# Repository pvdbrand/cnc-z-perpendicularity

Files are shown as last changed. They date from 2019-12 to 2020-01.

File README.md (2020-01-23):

# Automatically calibrating a CNC

## What's this?

The repository contains a Python script to automatically determine how perpendicular the Z axis of a CNC machine is, using just a feeler gauge and a touch probe.

This repository also contains a simulator (written in Rust) to make sure that the movements and calculations in the Python script are actually correct.

## How to use it

### Hardware

1. Build the arm:
   1. 3D print the [arm](https://github.com/pvdbrand/cnc-z-perpendicularity/blob/master/parts/arm.stl)
   1. Insert a needle in the clamp at the end, make sure it sticks out around 20-25mm below the arm
   1. Insert an M3 bolt in the hole close to the collet nut hole and connect the needle to this bolt with a piece of wire
   1. Mount the arm to the collet nut of your router and use another M3 bolt to secure it in place
1. Build the feeler gauge holder:
   1. 3D print the [holder](https://github.com/pvdbrand/cnc-z-perpendicularity/blob/master/parts/gauge_holder.stl)
   1. Wrap a piece of wire around the middle of feeler gauge
   1. Put a feeler gauge on top of the holder, put the lid on top, and screw it together with 4 M3 bolts
   1. Bolt the assembly to your spoil board, with the long end parallel to the X axis and the feeler gauge on the right-hand side
1. Attach the Z probe:
   1. One wire should be attached to the wire that is connected to the feeler gauge
   1. The other wire should be attached to the M3 bolt that is connected to the needle

This is how it looks when everything is assembled:
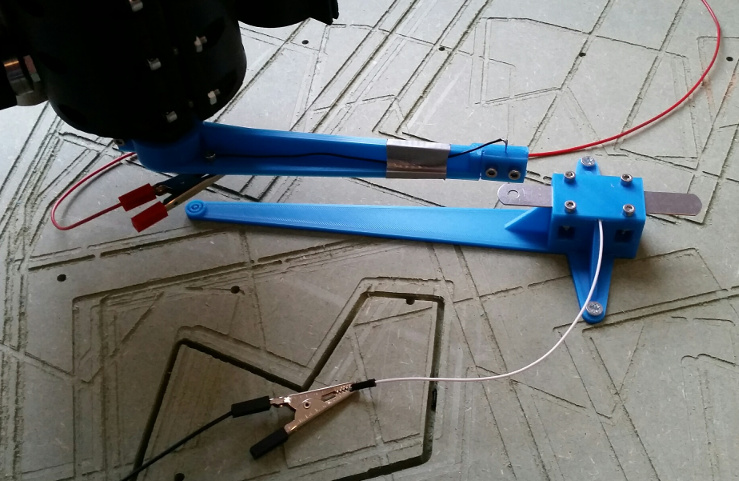
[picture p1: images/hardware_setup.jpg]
hardware setup


### CNC Firmware

The script only uses gcode to communicate with your CNC router. Any firmware that supports the required gcodes should work. It has only been tested with Marlin so far.

When using Marlin:

1. The Z probe should be wired and configured to trigger the `z_min` endstop. (It was the only way I could get `G28 Z` and `G38` to work at the same time. If yours is triggered by `z_probe`, then change `z_min` to `z_probe` in the `isZProbeTriggered` function.)
1. Enable `G38` in Marlin in `Conguration_adv.h`:
   1. Uncomment `#define G38_PROBE_TARGET`
   1. Uncomment `#define G38_PROBE_AWAY`
   1. Recompile and upload Marlin to your CNC router

### Software

1. For the simulator:
   1. Install [Rust](https://www.rust-lang.org/tools/install)
   1. In the simulator subdirectory, run `cargo build` or `cargo run`
   1. You can control the simulator with the keyboard
1. For the calibration script:
   1. Install Python 2.7, pandas, matplotlib, and statsmodels (you can use [Conda](https://docs.conda.io/projects/conda/en/latest/user-guide/install/) to make this easier)
   1. Edit the settings at the top of the script (below the imports) to your needs

### Running the script

1. Position the router as shown in the pictue above, with the arm parallel to the X axis and pointing towards positive X
1. Position the needle on top of the feeler gauge, a couple of millimeters to the right of the tip
1. Open [feeler_gauge.py](https://github.com/pvdbrand/cnc-z-perpendicularity/blob/master/feeler_gauge.py) in the Spyder IDE and run it. Alternatively, run `python feeler_gauge.py` from the command line
1. While the script is running, keep an eye on your machine to make sure it's not doing anything weird. The full script will take up to half an hour.
1. When it's done, it will print something like this:

`Spindle angle around X:  -0.1563 degrees off perpendicular`

`Spindle angle around Y:   0.2554 degrees off perpendicular`

`Z axis angle around X:    0.3192 degrees off perpendicular`

`Z axis to spindle in X:  -0.4756`

`Z axis angle around Y:    0.1866 degrees off perpendicular`

`Z axis to spindle in Y:   0.0688`

"Spindle angle around X/Y" means the angle between the XY plane and the tip of the end mill. If this is zero, surfacing your spoilboard would make it perfectly flat. If it's nonzero, you would get tiny ridges.

"Z axis angle around X/Y" means the angle between the XY plane and the movement of the Z axis. If this is zero, your Z axis moves up and down exactly vertically. If it's nonzero, it also moves laterally when moving up and down.

"Z axis to spindle in X/Y" is the difference between the former two angles. This is the amount you need to shim the router mount to get it perpendicular.

## The simulator in action

See [this video on Youtube](https://www.youtube.com/watch?v=3-CxL5ajJyM).

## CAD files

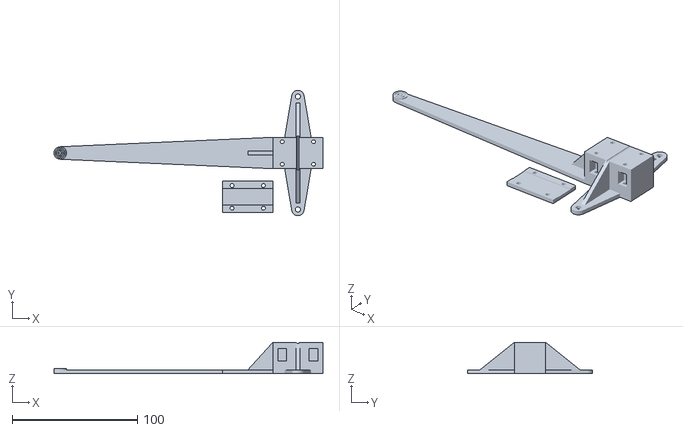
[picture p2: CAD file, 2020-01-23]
parts/gauge_holder.stl
214.5 x 100.0 x 25.0

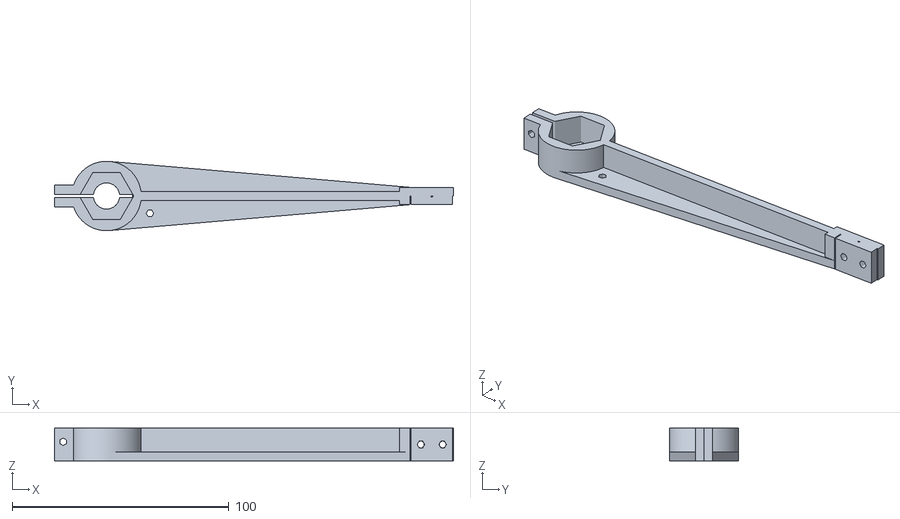
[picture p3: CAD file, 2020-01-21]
simulator/resources/arm.obj
184.0 x 32.0 x 15.0

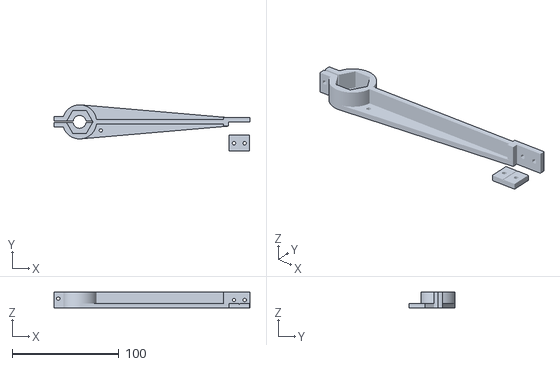
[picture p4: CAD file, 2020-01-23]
parts/arm.stl
184.0 x 43.5 x 15.0

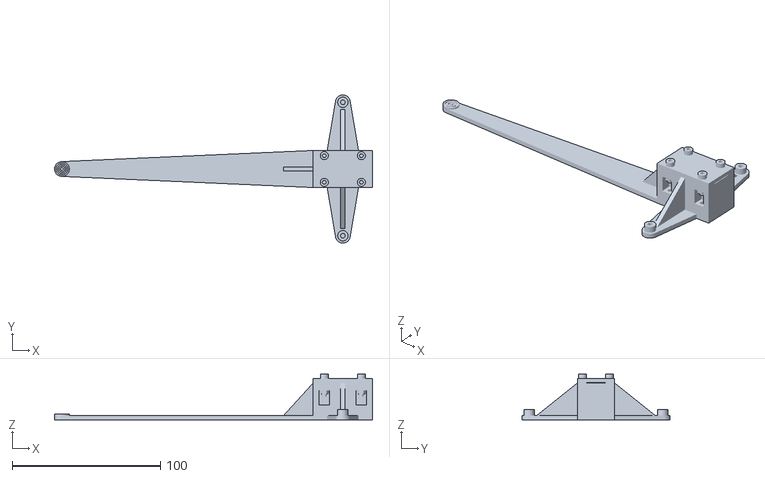
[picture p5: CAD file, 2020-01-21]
simulator/resources/gauge-holder.obj
214.5 x 100.0 x 31.0

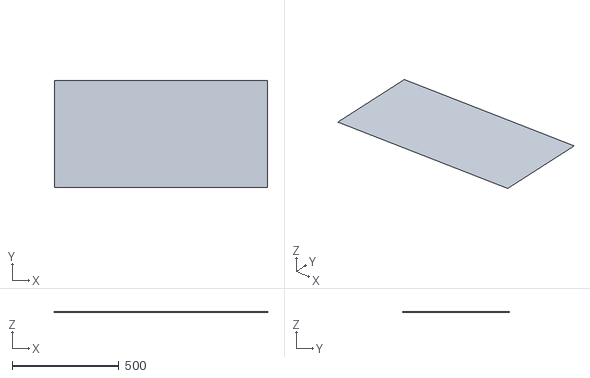
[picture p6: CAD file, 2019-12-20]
simulator/resources/spoilboard.obj
1000.0 x 500.0 x 1.00

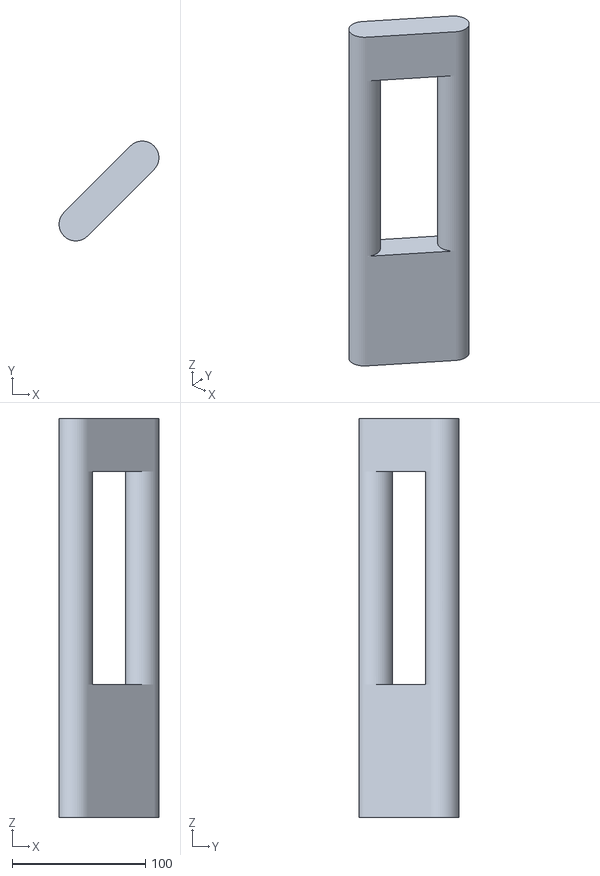
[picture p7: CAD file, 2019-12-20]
simulator/resources/z-axis.obj
75.0 x 75.0 x 300.0

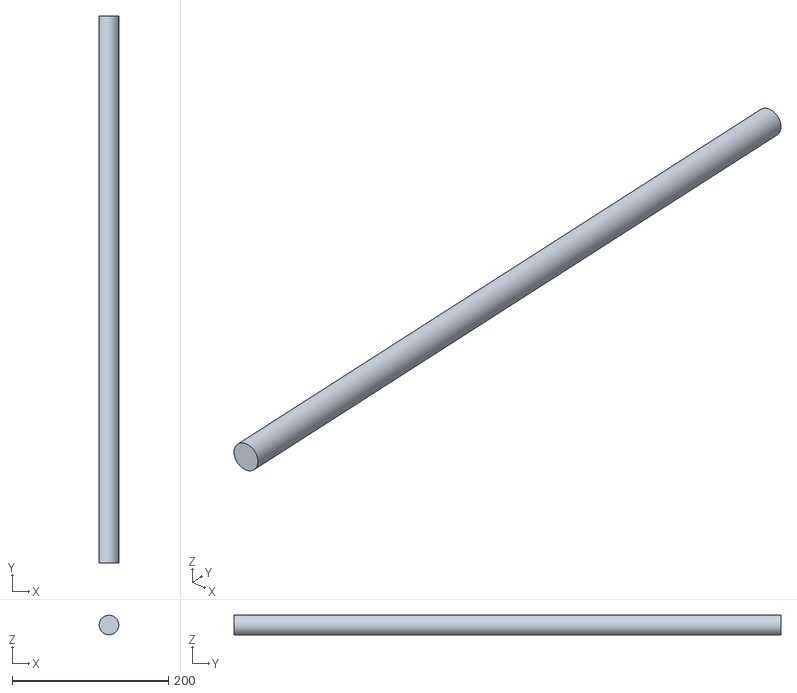
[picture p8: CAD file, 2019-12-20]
simulator/resources/gantry-x-tube.obj
25.0 x 700.0 x 25.0

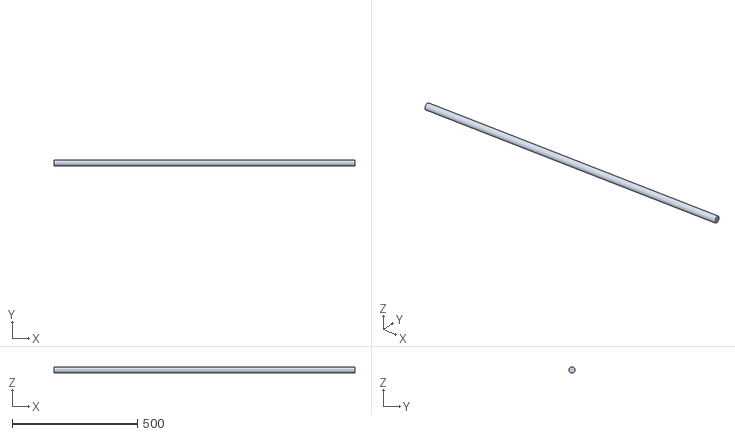
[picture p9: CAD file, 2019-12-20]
simulator/resources/gantry-y-tube.obj
1200.0 x 25.0 x 25.0

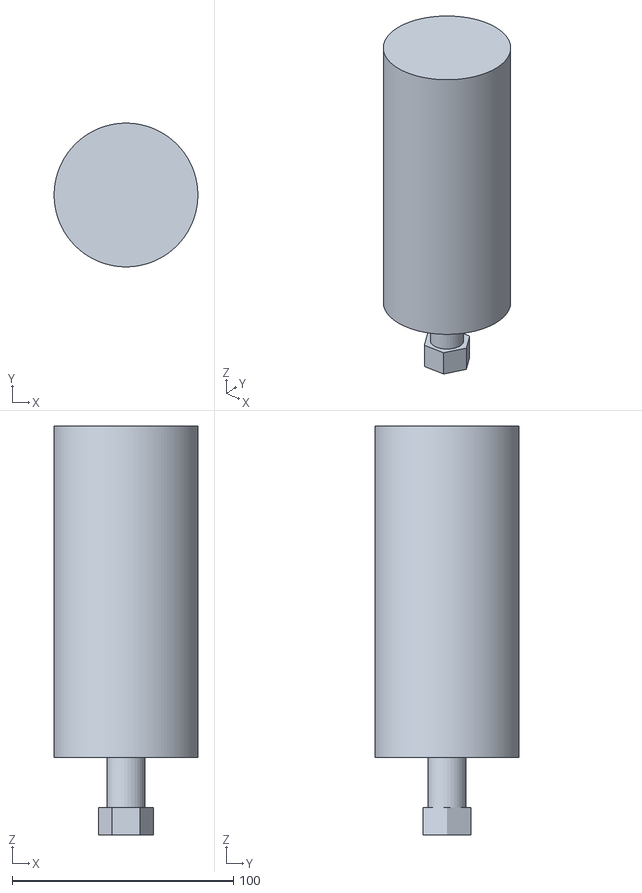
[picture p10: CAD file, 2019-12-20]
simulator/resources/spindle.obj
65.0 x 65.0 x 185.0

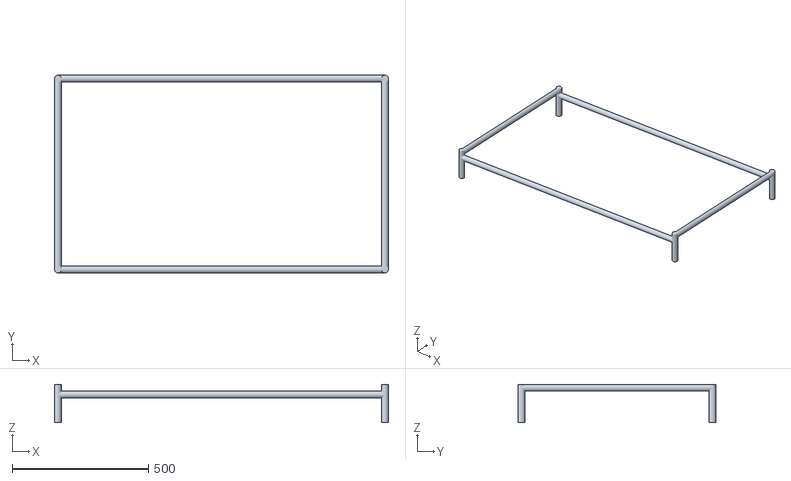
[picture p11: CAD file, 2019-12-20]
simulator/resources/frame.obj
1225.0 x 725.0 x 140.0

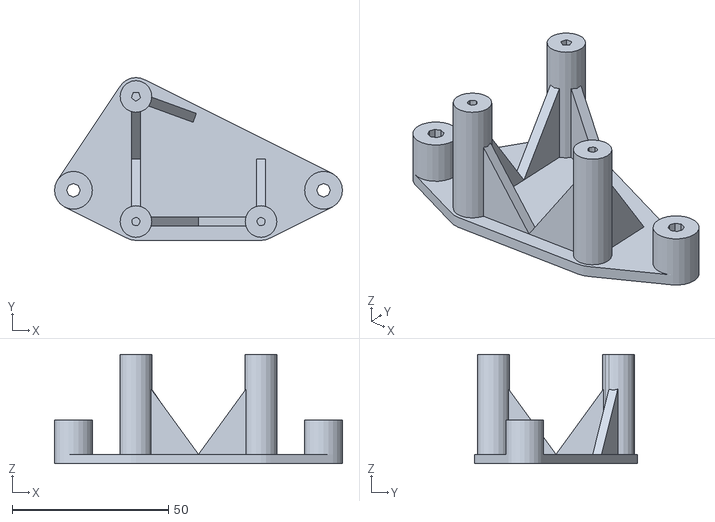
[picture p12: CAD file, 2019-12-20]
simulator/resources/calibration-object-plastic.obj
92.1 x 52.1 x 35.0

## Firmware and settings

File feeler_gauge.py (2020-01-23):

#!/usr/bin/env python2
# -*- coding: utf-8 -*-

import math, sys
import pandas as pd
import matplotlib.pyplot as plt
import statsmodels.api as sm
from scipy.interpolate import interp1d
from skimage.measure import EllipseModel
import matplotlib

from marlin import Marlin

useSimulator = True

simulator = {
    'executable': '/home/peter/github/cnc-z-perpendicularity/simulator/target/debug/simulator',
    'working_directory': '/home/peter/github/cnc-z-perpendicularity/simulator',
    'fast': True,
}

marlinPort = "/dev/serial/by-id/usb-Arduino__www.arduino.cc__0042_85531303231351E0E181-if00"
marlinBaudrate = 250000

feelerGaugeWidth = 13.0 # mm
feelerGaugeLength = 89.0 # mm
feelerGaugeThickness = 0.8 # mm
probeWidth = 4.0 if useSimulator else 0.8 # mm

approxLen = 150.0
approxAngle = 180.0

safeHeight = 7.5  # mm
safeDistance = feelerGaugeWidth / 2.0 + probeWidth / 2.0 + 5.0 # mm

zSpeed = 6 # mm/s
xySpeed = 10 # mm/s
probeSpeed = 2 # mm/s

numAngles = 6 # should be a multiple of 3

minProbeDistance = 1
probeDepths = [-14, -9, -4]
xOffsets = [4, 12] # [5, 10, 15]

minProbeDistanceRough = 5.0
probeDepthsRough = [-14, -4]
xOffsetsRough = [4, 12]

tipToCenter = 2.5 # mm
rotateHeight = min(probeDepthsRough)

###############################################################################

assert(numAngles % 3 == 0)
assert(numAngles >= 3)
assert(len(probeDepths) >= 2)
assert(len(xOffsets) >= 2)
assert(len(probeDepthsRough) >= 2)
assert(len(xOffsetsRough) >= 2)

pd.set_option('display.max_columns', 10)
pd.set_option('display.width', 125)

###############################################################################

marlin = Marlin(simulator if useSimulator else None)
marlin.connect(marlinPort, marlinBaudrate)

if useSimulator:
    startX = 500 + math.cos(math.radians(approxAngle)) * approxLen - (feelerGaugeLength / 2.0 - 0.0)
    startY = 250 + math.sin(math.radians(approxAngle)) * approxLen
    if 0:
        marlin.send('M800 A0.5  B0.25')
        marlin.send('M801 A1    B0.5   R%d' % (approxAngle - 180))
        marlin.send('M802 A0.5  B1     O%f' % approxLen)
        marlin.send('G1 X%d Y%d' % (startX, startY))
    elif 1:
        marlin.send('M800 A0.05 B0.17')
        marlin.send('M801 A0.13 B0.23 R%d' % (approxAngle - 180))
        marlin.send('M802 A0.03 B0.07 O%f' % approxLen)
        marlin.send('G1 X%d Y%d' % (startX, startY))
    elif 0:
        marlin.send('M800 A0.07 B0')
        marlin.send('M801 A0.23 B0 R%d' % (approxAngle - 180))
        marlin.send('M802 A0.00 B0 O%f' % approxLen)
        marlin.send('G1 X%d Y%d' % (startX, startY))
    elif 0:
        marlin.send('M800 A0 B0')
        marlin.send('M801 A0 B0 R%d' % (approxAngle - 180))
        marlin.send('M802 A0.03 B0.07 O%f' % approxLen)
        marlin.send('G1 X%d Y%d' % (startX, startY))
    else:
        marlin.send('M800 A0 B0')
        marlin.send('M801 A0 B0 R%d' % (approxAngle - 180))
        marlin.send('M802 A0 B0 O%f' % approxLen)
        marlin.send('G1 X%d Y%d' % (startX, startY))
    marlin.home()

if not marlin.isZProbeTriggered():
    print 'Error: Z probe is not triggered.'
    print 'Make sure the router is in the correct starting position, and that the Z probe is triggered.'
    sys.exit(0)

marlin.enableSteppers()
marlin.setPosition(0, 0, 0)
marlin.go(0, 0, safeHeight, mm_per_second=zSpeed, wait=True)

if marlin.isZProbeTriggered():
    print 'Error: Z probe is still triggered after trying to move up. Please check your probe.'
    sys.exit(0)

    
def find_center(xOffsets, probeDepths, minProbeDistance, leftSide=True):
    global marlin, safeHeight, approxAngle, tipToCenter, probeWidth
    
    cx, cy, cz = marlin.getPosition()
    assert(cz >= safeHeight)
    
    direction = 1 if leftSide else -1
    
    ########################################
    # Probe the front and back

    front_back = []
    for side in [-1, 1]:
        y = side * safeDistance + cy
        
        xs = [cx + offset * direction for offset in xOffsets]
        if side > 0:
            xs = list(reversed(xs))

        for x in xs:
            _, _, z = marlin.getPosition()
            marlin.go(x, y, z, mm_per_second=xySpeed)
                
            for z in probeDepths:
                marlin.go(x, y, z, mm_per_second=zSpeed, wait=True)
                assert(not marlin.isZProbeTriggered())
            
                _, y, _ = marlin.probe(x, cy, z, mm_per_second=probeSpeed, towards=True)
                sideLabel = 'front' if side < 0 else 'back'
                front_back += [{'x': x, 'y': y, 'z': z, 'side': sideLabel, 'leftSide': leftSide, 'ok': marlin.isZProbeTriggered()}]
                y = y + side * minProbeDistance
        
                marlin.go(x, y, z, mm_per_second=xySpeed)
        marlin.go(x, y, safeHeight, mm_per_second=zSpeed)
    front_back = pd.DataFrame(front_back)

    # fit a (vertical) plane through the centerline of the gauge at different Z heights
    # Given X and Z, find the Y of the plane
    # y = c + ax + bz + epsilon
    plane = front_back.groupby(['z', 'x'])[['y']].mean().reset_index()
    plane['c'] = 1.0
    plane = sm.OLS(plane['y'], plane[['c', 'x', 'z']]).fit()
    if 0:
        print plane.summary()
    
    ########################################
    # Probe the side

    side = []
    x = cx - safeDistance * direction
    marlin.go(x, cy, safeHeight, mm_per_second=xySpeed)
    for z in probeDepths:
        centerline = front_back[front_back['z'] == z].groupby('x')[['y']].mean().reset_index()
        centerline['c'] = 1.0        
        model = sm.OLS(centerline.y, centerline[['c', 'x']]).fit()
        center_y_at_cx = model.params['c'] + model.params['x'] * cx
        center_y_at_x = model.params['c'] + model.params['x'] * x

        marlin.go(x, center_y_at_x, z, mm_per_second=zSpeed, wait=True)
        assert(not marlin.isZProbeTriggered())
    
        x, y, _ = marlin.probe(cx, center_y_at_cx, z, mm_per_second=probeSpeed, towards=True)
        side += [{'x': x, 'y': y, 'z': z, 'side': 'side', 'leftSide': leftSide, 'ok': marlin.isZProbeTriggered()}]
        x -= minProbeDistance * direction

        marlin.go(x, center_y_at_x, z, mm_per_second=xySpeed)
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

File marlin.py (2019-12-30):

#!/usr/bin/env python2
# -*- coding: utf-8 -*-

import serial
import time
import subprocess

class Marlin:
    def __init__(self, simulator=None):
        self.simulator = simulator
        
    def connect(self, port, baudrate, timeoutSeconds=30, waitSeconds=8):
        if self.simulator is not None:
            command = [self.simulator['executable'], "--no-keyboard"]
            if self.simulator['fast']:
                command += ["--fast"]
            self.conn = subprocess.Popen(command,
                            cwd=self.simulator['working_directory'],
                            stdin=subprocess.PIPE,
                            stdout=subprocess.PIPE)
        else:
            self.conn = serial.Serial(port, baudrate, timeout=timeoutSeconds)
            time.sleep(waitSeconds)
            self.conn.flushInput()
        
        # first command sent can be garbled, so send something that doesn't do anything
        self.send('M110 N0')
        
        # Make sure we can communicate properly now
        x, y, z = self.getPosition()
        assert(x is not None and y is not None and z is not None)

        self.send('G90')

    def close(self):
        if self.simulator is not None:
            self.conn.stdin.close()
            self.conn.stdout.close()
            self.conn.kill()
        else:
            self.conn.close()
        self.conn = None
        
    def go(self, x, y, z, mm_per_second=8, rapid=False, wait=False):
        command = 'G0' if rapid else 'G1'
        self.send('%s X%f Y%f Z%f F%f' % (command, x, y, z, mm_per_second * 60))
        if wait:
            self.waitUntilStopped()

    def probe(self, x, y, z, mm_per_second=8, towards=True):
        command = 'G38.2' if towards else 'G38.4'
        for attempt in range(3):
            self.send('%s X%f Y%f Z%f F%f' % (command, x, y, z, mm_per_second * 60))
            self.waitUntilStopped()
        return self.getPosition()

    def rotateArm(self, x, y, z, clockwise, mm_per_second=8, wait=False):
        command = 'G1' if self.simulator is None else ('G38.8' if clockwise else 'G38.9')
        self.send('%s X%f Y%f Z%f F%f' % (command, x, y, z, mm_per_second * 60))
        if wait:
            self.waitUntilStopped()

    def enableSteppers(self, x=True, y=True, z=True):
        self.send('M17%s%s%s' % (' X' if x else '', ' Y' if y else '', ' Z' if z else ''))

    def disableSteppers(self, x=True, y=True, z=False):
        self.send('M18%s%s%s' % (' X' if x else '', ' Y' if y else '', ' Z' if z else ''))

    def setPosition(self, x, y, z):
        self.send('G92 X%f Y%f Z%f' % (x, y, z))

    def home(self, axis='Z'):
        self.send('G28 %s' % axis)

    def waitUntilStopped(self):
        self.send('M400')
        
    def getPosition(self):
        return self._parsePosition(self.send('M114'))
        
    def isZProbeTriggered(self, pin='z_min'):
        response = self.send('M119')
        for line in response.split('\n'):
            if line.startswith(pin + ': '):
                return 'TRIGGERED' in line
        return None
        
    def send(self, line):
        outputStream = self.conn if self.simulator is None else self.conn.stdin
        outputStream.write(line.strip() + '\n')
        return self._receive()
        
    def _receive(self):
        inputStream = self.conn if self.simulator is None else self.conn.stdout
        result = ''
        while True:
            line = inputStream.readline().strip()
            if line is None:
                raise Exception('Connection closed while waiting for response')
            if line == 'ok':
                break
            if not line.startswith("echo:busy:") and not line.startswith("busy:") and not line.startswith("//"):
                result += line + '\n'
        return result

    def _parsePosition(self, line):
        fields = {}
        while ':' in line:
            label, line = line.split(':', 1)
            value, line = line.split(' ', 1) if ' ' in line else (line, '')
            line = line.strip()
            if label not in fields:
                fields[label] = float(value)
        return (fields.get('X', None), fields.get('Y', None), fields.get('Z', None))

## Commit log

2019-12-16 3D printable tool
    [perpendicularity-tool.stl]
2019-12-17 Image of probe setup
2019-12-19 First version of simulator
    [base.obj, endmill.obj, gantry-x-tube.obj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]
2019-12-19 Corrected rotation and travel limits
    [base.obj, endmill.obj, frame.obj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]
2019-12-19 Added calibration object
    [calibration-object-metal.obj, calibration-object-plastic.obj]
2019-12-19 Implemented Z probe against wires
2019-12-20 Use f64 for thinner wires
2019-12-20 Implemented probe_towards
2019-12-20 Started with gcode
    [calibration-object-metal.obj, calibration-object-plastic.obj, endmill.obj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]
2019-12-20 Clean up obj files
    [frame.obj, gantry-x-tube.obj, gantry-y-tube.obj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]
2019-12-20 Implemented relevant gcodes
    [spoilboard.obj]
2019-12-23 Added arm to spindle
    [arm.obj]
2019-12-30 Rotate arm
2019-12-31 Compute Z axis angle
2020-01-21 Update obj files
    [arm.obj, gauge-holder.obj]
2020-01-23 Fix Z axis angle around Y
    [feeler_gauge.py]
2020-01-23 3D printed parts
    [arm.stl, gauge_holder.stl]
